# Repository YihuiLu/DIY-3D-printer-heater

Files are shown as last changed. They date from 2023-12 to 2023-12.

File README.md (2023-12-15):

# DIY-3D-printer-heater
一个简单好用的3D打印机仓温加热模块

>### **视频来源**：[Bilibili@我是小一灰](https://www.bilibili.com/video/BV1Na4y1G7fo "我是小一灰")
>### QQ交流群：940677189、339148314（2群）
> ### **Gitee（国内）项目地址**：[3D打印机仓温加热模块]( "我是小一灰")
> ### **Github项目地址**：[3D打印机仓温加热模块]( "我是小一灰")

##### 配置文件、接线图、打印件等等都在项目里寻找就可以了，打印件我直接公开了源文件，大家随意修改
#### 配置文件修改教程：
```buildoutcfg
首先注释掉你原有的舱温传感器配置
#[temperature_sensor 仓温]
## sensor_type: NTC 100K MGB18-104F39050L32
#sensor_type: Generic 3950
#sensor_pin: PA2
#pullup_resistor:4700
如果你本来就没有舱温传感器，那就忽略，下方配置从舱温传感器中取的值，你自己找空余接口就行，分别是空闲的热敏接口、加热棒接口
接口的pin值需要你自己查阅你主板的pin图，如果你不知道什么是pin图，咨询你的主板卖家。

[heater_generic hot]
#这一段完整的加到配置文件
heater_pin:PE1  # 修改为任意一个闲置加热棒端口（这里以M8P脚位为例）
max_power:1.0
sensor_type:NTC 100K MGB18-104F39050L32 # 修改为你舱温传感器型号
sensor_pin:PA2  # 修改为你舱温传感器sensor_pin的值
control = watermark
max_delta: 1.0
min_temp:-50
max_temp:70

[verify_heater hot] #舱温的名字不能随便改
#这一段完整的加到配置文件
max_error: 300
check_gain_time:480
hysteresis: 5
heating_gain: 1

[gcode_macro M141]
#这一段完整的加到配置文件
gcode:
      SET_HEATER_TEMPERATURE HEATER=hot TARGET={params.S}

[gcode_macro PRINT_END]
gcode:
    ...
    ...    
    #以上你的原有配置不要动
    M141 S0  # 就把这一行，加到你的[gcode_macro PRINT_END]配置项里，目的是在打印结束时，自动停止加热
    #以下你的原有配置不要用
    ...
    ...

[gcode_macro CANCEL_PRINT]
#如果你有取消打印宏，别忘了把M141 S0加到取消打印宏里

```
----
>视频里演示的加热器是200W的，加热器本身的温度在150度左右，你可以更换更大功率的加热器，仓温可以加到很高，但你可以通过配置文件限制安全温度
> 
> 
###物料清单（Voron2.4）：

| 项目 | 数量 | 链接 | 备注 |
| --- | --- | --- | --- |
| 220V 200W 长条PTC加热器  | 1  | 暂无  | 视频中使用的尺寸是140×35×️26mm，可以把仓温加热到70度左右，其他功率尺寸可能要改模型  |
| 5015风扇  | 1  | 暂无  |Voron SB头那种  |
| M3垫片  | 4  | 暂无  |  |
| M3*6杯头螺丝  | 6  | 暂无  |  |
| M3船形螺母  | 4  | 暂无  |型材用的船形螺母  |
| M3螺母  | 2  | 暂无  |6边形螺母  |
| 导线  | 若干  | 暂无  |注意功率  |
| 固态继电器  | 1  | 暂无  |问问卖家能不能带动你买的加热器功率  |
| NTC 100K热敏  | 1  | 暂无  |如果你没有仓温热敏，买这个  |

###物料清单（Voron三叉戟）：

| 项目 | 数量 | 链接 | 备注 |
| --- | --- | --- | --- |
| 220V 200W 方形加热器  | 1  | 暂无  | 带220v风扇的，功率随意  |
| M4*40杯头螺丝  | 2  | 暂无  |  |
| M3杯头螺丝  | 2  | 暂无  |  |
| M3船形螺母  | 2  | 暂无  |型材用的船形螺母  |
| 导线  | 若干  | 暂无  |注意功率  |
| 固态继电器  | 1  | 暂无  |问问卖家能不能带动你买的加热器功率  |
| NTC 100K热敏  | 1  | 暂无  |如果你没有仓温热敏，买这个  |

接线图在目录中找PDF文件
2.4接线图
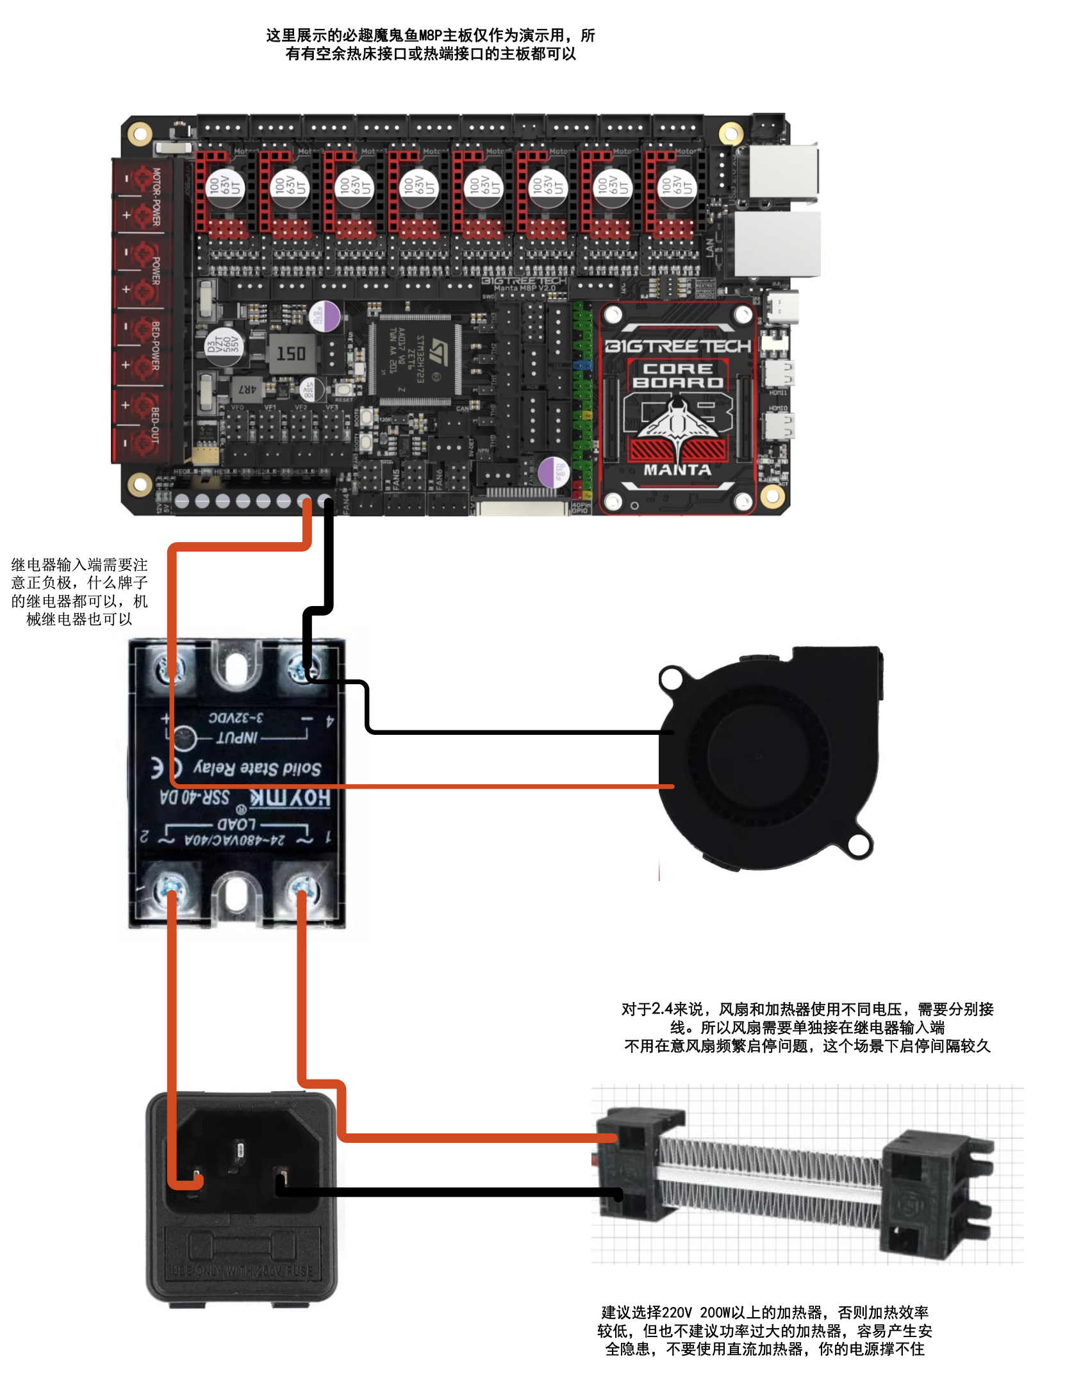
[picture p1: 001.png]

三叉戟接线图
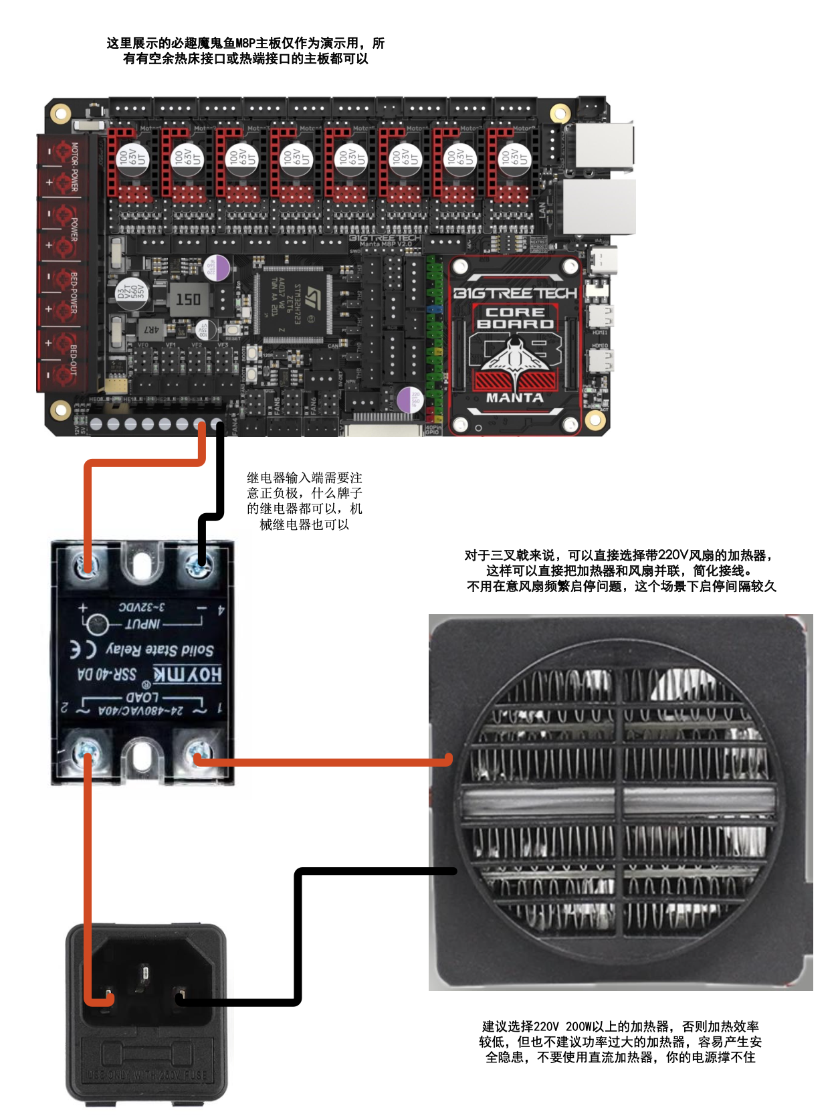
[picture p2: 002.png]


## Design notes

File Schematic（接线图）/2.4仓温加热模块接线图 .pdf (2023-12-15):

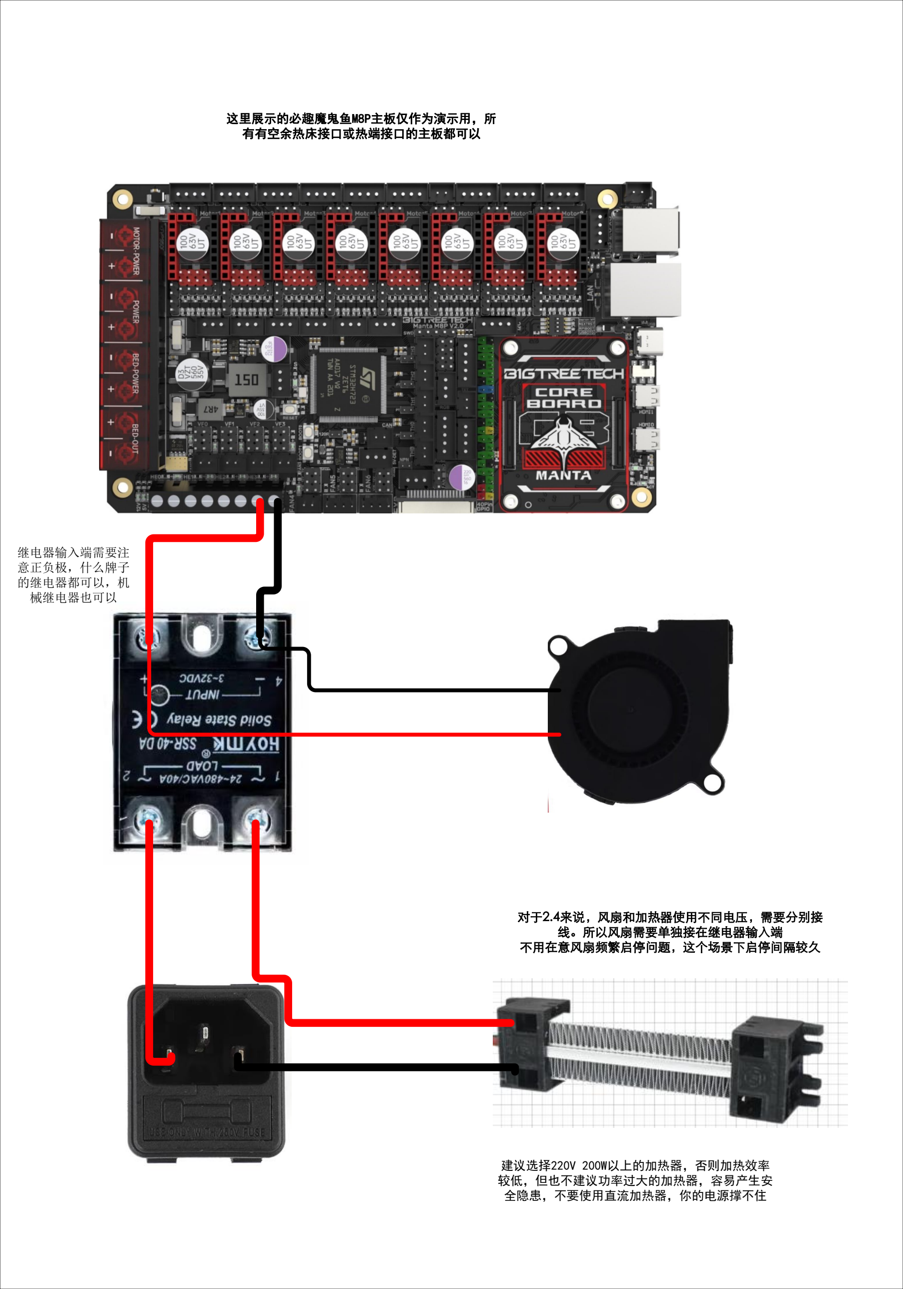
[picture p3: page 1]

对于2.4来说，风扇和加热器使用不同电压，需要分别接 线。所以风扇需要单独接在继电器输入端
不用在意风扇频繁启停问题，这个场景下启停间隔较久

继电器输入端需要注
意正负极，什么牌子
的继电器都可以，机
械继电器也可以

建议选择220V 200W以上的加热器，否则加热效率 较低，但也不建议功率过大的加热器，容易产生安
全隐患，不要使用直流加热器，你的电源撑不住

这里展示的必趣魔鬼鱼M8P主板仅作为演示用，所
有有空余热床接口或热端接口的主板都可以

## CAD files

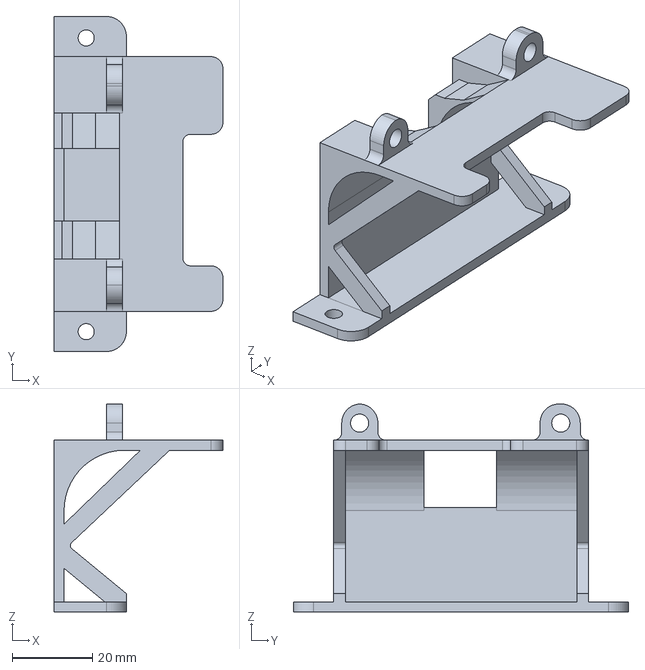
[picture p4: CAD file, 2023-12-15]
STLs（打印件）/voron三叉戟仓温支架.step
42.0 x 83.3 x 51.7 mm

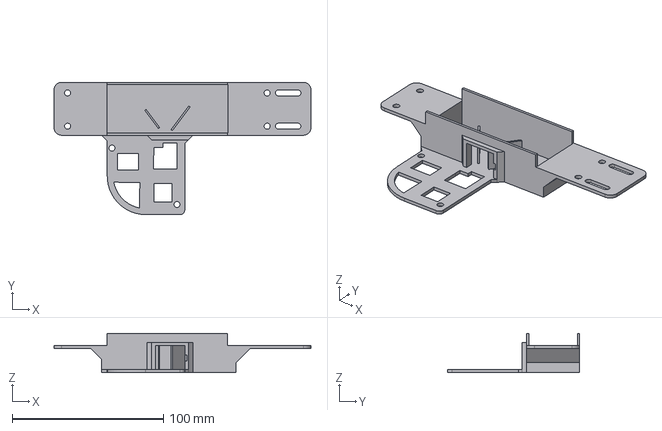
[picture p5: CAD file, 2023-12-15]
STLs（打印件）/2.4仓温支架.step
170.0 x 87.5 x 26.0 mm

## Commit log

2023-12-15 2.4、三叉戟仓温模块
2023-12-15 增加打印件源文件
    [2.4仓温支架.step, voron三叉戟仓温支架.step]
